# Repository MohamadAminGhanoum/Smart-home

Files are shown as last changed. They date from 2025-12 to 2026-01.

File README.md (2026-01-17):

[BOM - Smart home - BOM.csv](https://github.com/user-attachments/files/24395662/BOM.-.Smart.home.-.BOM.csv)
ESP32 - Smart home project:
--------------------------------
Project description:
This project is a custom-built ESP32-based control to automate a curtain motor and manage multiple devices in my room such as a fan, LED strip, temperature sensor, and additional motors. This is buit using a custom PCB designed in KiCad, using only salvaged components from old electronics but also used Arduino uno for the code

Video: https://www.youtube.com/shorts/h7QkvN7-KNk

The project focuses mainly on hardware design, PCB routing and building in Kicad, reusing components, and experimentation, but not so much software work.
"Note, the main code is not fully written by me, and it is not the main focus of this project. It is only here for reference or experimenting."

Why i mainly made this project:
I wanted to make this project to:
- Learn how to design PCB
- Searching schematics for components and reusing the components from devices
- Build something practical that i can use in my everyday life.

Below is the schematic diagram: Note: im missing 2 resistors, since i could not find the exact symbol for the motor driver that was in the robot-vacuum board.


Below is the pcb that i etched myself:
PCB - etched

This is the wiring diagram of the pcb:
Final pcb

These are all materials that i used in the project, u can also access it in the repo
Screenshot_31-12-2025_161940_docs google com

Final reflection
-------------------------------------------
I think that this project for me honestly was difficult. This was my first time using kicad to create a pcb and schematic, and i did some issues, like forgetting to make a schematic and jumping directly to pcb. I had to do many retries to get to my final result. I did much experimenting with trasferring the ink from paper to pcb. I ended up printing the pcb-layout on the paper 3 times through printer, since i twas a normal paper

I further also did not log the hours that i took me to find the ldo voltage regulator from a motherboard, and the time taken to research the different parts from the robot vacuum, because i dont think this counts.

I finally did enjoy making this project, and it was both entertaining and taught me how pcbs are made. If i had to redo this, I think i would put money in getting glossy paper, because they would have made this a lot easier by transferring the ink from the printer directly to pcb.

This project was overall successful, although I had some errors and mistakes. It hepled me with learning how to make PCBs, how to reuse unknow parts by lookin in their schematics, how to connect the ESP32, and at last it needed a lot of creativity to work.

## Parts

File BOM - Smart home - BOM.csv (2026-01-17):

Name: | Part nr: | Price: | Quantity: | Function: | Link:
ESP32 | ESP32-Wroom | 0 | 1 | To control and connect to wifi
CeramicCapacitors | 1uF | 0 | Multipe | Stabilize voltage | From laptop motherboard
Electrolytic capacitors | 100uF, 25V | 0 USD | 2 | For power smoothing | From robot vacuum
Curtain motor | (Wheels of vacuum) | 0 USD | 2 | Open/close curtain | From robot vacuum
Motor driver | AM4659 | 0 USD | 2 | to drive the motor | From robot vacuum
Fan | 5v Fan | 0 USD | 1 | prevent solder smoke/ventilate | From pc
LED strip | 5V old LED strip | 0 USD | 1 | to light the room | Laying around
Thermistor | 10 kohm NTC | 0 USD | 1 | Measure temperature | From laptop cpu temp sensor
Mosfet | G961 1A LDO | 0 USD | 1 | To control brightness of LED strip | https://www.alldatasheet.com/datasheet-pdf/view/105493/GMT/G961-18ADJTEU.html
Copper Clad | to have pcb on it | 7 dollar | 5 | To put components on | https://www.aliexpress.com/item/1005006221193001.html?curPageLogUid=TUCw4VrV8onk
Wires | any type of wire | 0 USD | Multiple | to connect the connectors | Any type of wire
Resistor, pull up | 10 kohm | 0 USD | 1 | Voltage divider for thermistor | Had it laying around
Resistor | 0.1 ohm, 1W | 0 USD | 2 | Current sensing for the AM4659 | Any resistor under 1 ohm
Input protection | ET9528 | 0 USD | 1 | Overvoltage & overcurrent protection | https://etek.com.cn/upload/files/product/20250630/17512731716326659.pdf

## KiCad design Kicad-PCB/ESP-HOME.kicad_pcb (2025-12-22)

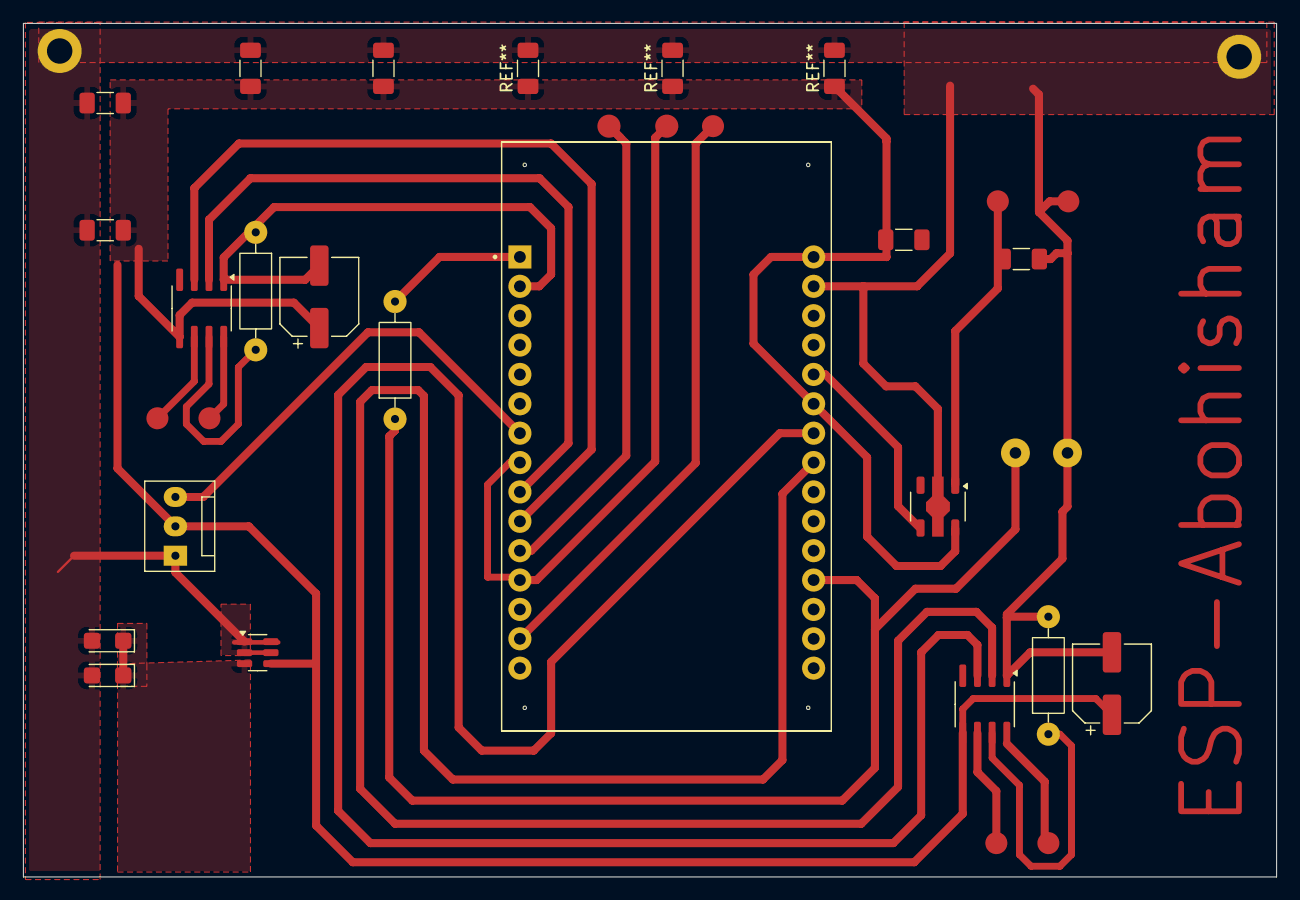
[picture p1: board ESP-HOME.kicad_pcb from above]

Board: 2 copper layers, 108.4 x 73.8 mm, 3 parts (0 on the bottom side), 3 nets.

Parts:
M2: Fan_3pin; FanPinHeader_1x03_P2.54mm_Vertical
TH1: Thermistor
U1: ESP32-DEVKIT-V1; MODULE_ESP32_DEVKIT_V1

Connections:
GND: M2.1 (-), TH1.1, U1.2 (GND), U1.29 (GND)
unnamed: TH1.2, U1.19 (D34)
g: M2.2 (+), U1.25 (D27), U1.30 (VIN)

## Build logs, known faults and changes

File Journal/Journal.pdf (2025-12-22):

## Routed main parts of curtain to pcb

I started this project by routing the curtain motor, that i extracted fron an old robot vacuum, and got that connected to the pcb, and i did some research, by trying to find schematics on different chips from the vacuum-motherboard and found a motor-controlling chip. I added it to my pcb on kicad, and luckily this chip was a 4-pin chip, which was a AM4959. This chip, I could give command to with two gpio pins from ESp-32, which provides 3.3v to make the motor rotate left or right. This was helpful, because now it is not necessary to use two motors, one to open and one to close the curtain.

It took quite some time to find the chip of the ESP32 controller, because it was not in the kicad library, so had to go through many websites to find the chip.

I added some capacitors

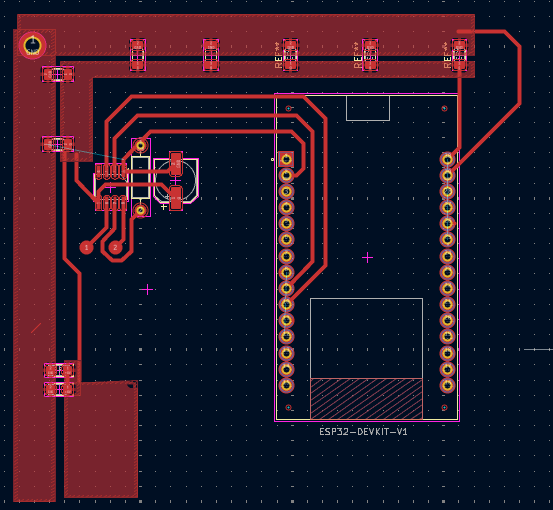
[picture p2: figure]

for stabilizing the voltage so it does not drop at the ESP32 when the motor draws current.

I used a bit of time to get the motor to stick to the wall, and make it pop a bit to the front, so it does not touch the frame of the window. It also took time to use a string from my mom's sewing things and tighten it to the motor, and test if the motor will open and close the curtain using a 5v power supply(originally a phone cable)
curtain motor

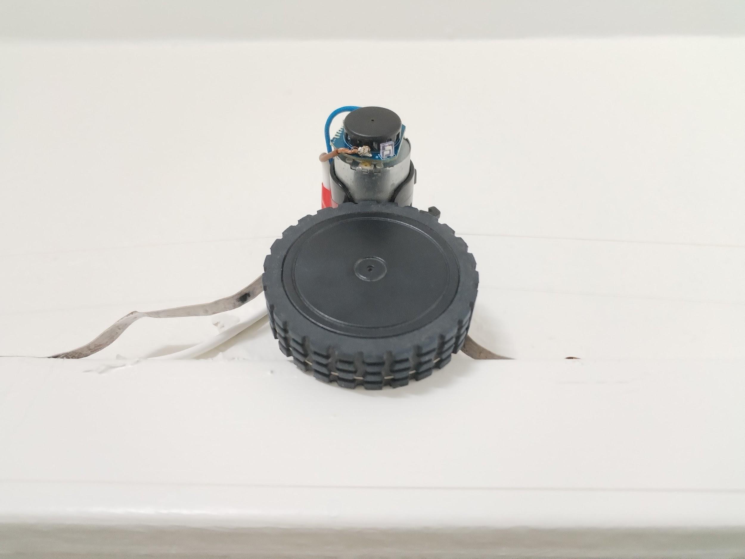
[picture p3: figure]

## added a fan

This time i added a fan to the pcb to control. This fan, i got from an unused desktop, and it didn not need a controller, so i connected one of the pins directly to the gpio pin and two others to gnd and +5v.

I thought that this fan can be used to take the smoke away, when im using the soldering iron, so i do not inhale the smoke.

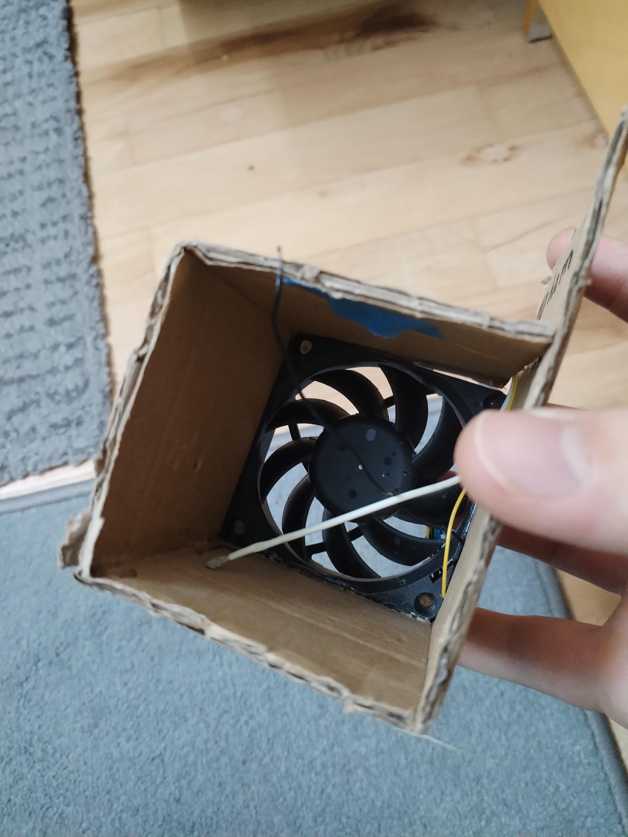
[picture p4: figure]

## Added temperature sensor

I now added a temperature sensor, or more coorect, a thermistor, which can be calibrated to measure temperature, im thinking by putting it in ice, and make the code so it tells that it is 0 degrees.

It was at first a struggle to connect the resistor and thermistor, because they needed a 3v3 volt connection and there was a track standing in my way, but then i got "a blessing", and thought, why not but the resistor there, so it jumps over the track. This actually helped and i could continue with this project.

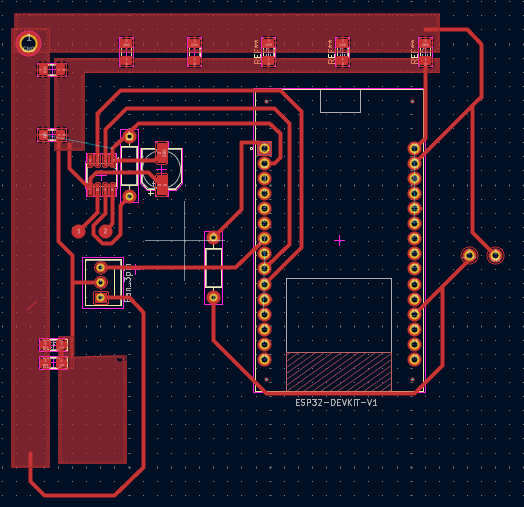
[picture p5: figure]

## Connected LED strip and one more motor + reroute pcb

Before i began this project, i had an led strip connected to my wall, but i had it
connected to 5v, phone charger, so everytime i needed to turn it on, i had to connect the charger.

So i thought i should add it to my project, and it was a great idea. But my issue now is to find a mosfet that can regulate the voltage by using the gpio pin as a gate. The issue here was than when i looked in a motherboard, i only found mosfets that needed 4.5v to open the mosfet, however the esp32 only provides 3.3v, so i did a very deep search into that motherboard. It really drained me.

I finally found a chip after looking in that motherboard across 2 days. it took longer than i expected.Now i can use the esp32 to control the voltage output to the 5v LED strip. It was pretty cool.

I then added another motor, just like the one from the first to control the curtain, but this motor, i did not really know what to use it for, but wanted it included for future ideas.

This took a good amount of time to get the components connected, and i had to reroute the pcb so all the components could fit inside.

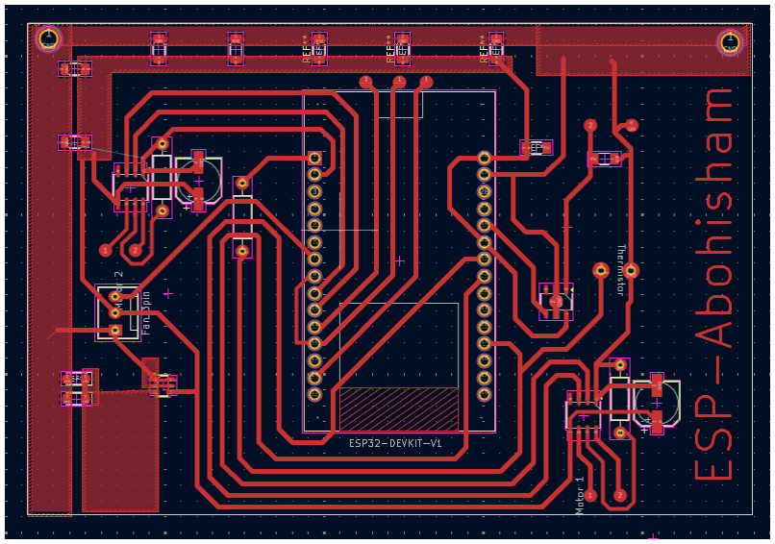
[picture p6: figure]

## Etched pcb, before buying one from pcbway

I did not want to use money to buy a new pcb, where I can have connected something wrong, therefore i wanted to try etching the pcb while trying out something new.

I soldered the components to the etched pcb, and could finally put code to control the esp32.
Though since i do not have so much knowledge about the coding, it was not fully written by me, thought the focus of this project is on the hardware building.

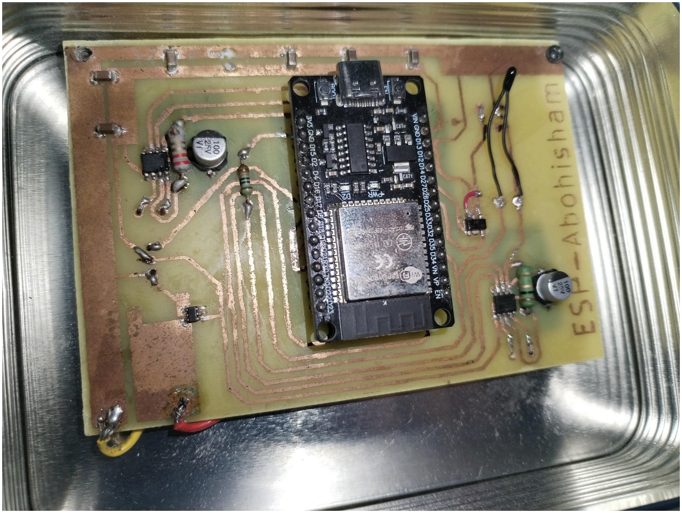
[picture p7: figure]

I found an error in my connection, and got lucky that i could fix it with the red wire.

This project in general was sucessful, but i had some errors.
Some of them was that i had a big drill, that made the holes large, and i connected the esp32 from above, could not do it from below because i did not mirror the ESP32 in kicad. Therefore this resulted in difficulties in soldering and the esp32 is unstable sometimes, if the casing falls, the connection breaks at 5v, so i have to solder again.

Therefore im thinking, i will definetly buy a pcb on pcbway later or from something similar, idk yey.

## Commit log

2025-12-19 Create Main code
    this is the code i uploaded to esp32
2025-12-22 Revise README with project details and components
    Expanded project description with detailed components and functionality, including motor, fan, temperature sensor, LED strip, and PCB etching process.
2025-12-22 Enhance README with project details and components
    Updated README to provide detailed project description, objectives, and component list for the ESP32 smart home project.
2025-12-22 Add project journal detailing hardware development
    Documented the process and challenges faced while building a project involving a curtain motor, fan, temperature sensor, LED strip, and PCB etching.
2025-12-22 Revise README to mention Arduino Uno integration
    Updated project description to include Arduino Uno usage.
2025-12-23 Update README with schematic and PCB diagrams
    Added schematic and PCB images to README.
2025-12-23 Update README with note on schematic diagram
    Added a note about missing resistors in the schematic diagram.
2026-01-17 Update and rename BOM - Smart home - BOM.csv to Kicad-PCB/BOM - Smart home - BOM.csv
    [BOM - Smart home - BOM.csv]
2026-01-17 Update and rename Kicad-PCB/BOM - Smart home - BOM.csv to BOM - Smart home - BOM.csv
    [BOM - Smart home - BOM.csv]
